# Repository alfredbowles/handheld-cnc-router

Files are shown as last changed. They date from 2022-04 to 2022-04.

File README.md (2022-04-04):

# Handheld CNC Router - Frebujar

The handheld CNC router is a project developed by Alfred Bowles, Shamanth Thenkan & Vincent Verster for a 2 month hardware seminar at the Institute for Advanced Architecture of Catalonia

The project aim is to develop a handheld CNC router which could be used for milling and inscribing into planar msheets of material.
The router will be hand-guided by the user while motors which control the position of the mill bit will activate to correct for the error made by the user between the actual and target position of the bit.

# Hardware & Materials #

All part drawings, milling files, and lasercutting files are found in the 'Manufacturing' dirctory.
BOM is found in the hardware folder

### Complete Assembly ###
* 4x Milled - Particle board, laminated on both sides : Thickness = 10mm
* 3x Lasercut - Plexiglass : Thickness = 6mm
* 2x Radial ball bearings : ID = 10mm
* 2x Radial ball bearings : ID = 50mm
* 2x Linear Bearings: ID = 10mm (For z-axis movement)
* 10mm thick calibrated steel rod
* 1x Shaft support
* 1x Threaded shaft bearing
* Various 3D Printed parts

LabeledPrototypeWhite

### Control, Power and Actuation ###
* 1x Raspberry Pi 4
* 1x Arduino Uno
* 1x 8MP Raspberry Pi Camera Module v2.1
* 1x Waveshare Raspberry Pi LCD Screen 3.5inch
* 3x Nema 17 Stepper Motors
* 3x A4988 Stepper Motor Drivers
* 1x 5v Fan
	


# Use Process

The user would either print or draw the desired pattern to be routed onto the piece of material. He would then activate the router and pass it over the material approximately following the printed path. The mounted camera which is aimed at the region around the bit tip will calculate the deviation needed to be made to account and correct for the user error and order the motors to move the mill head to the calculated point. As the user progresses through the material only the black areas which were printed or drawn will be removed and the piece would be complete.

# Control & Instructions

Since we are using a double cam mechanism we need to calculate how the bit would move with respect to the given motor rotations. In order to calculate the bit deviation, we use trigonometry and the law of cosines and sines.

### Angle Calculation ###
This code attempts to solve for those angles. (Angle calculation still to be optimized):
* Final_motion_calculation.py

The variables defined in the code are shown in the below diagram:
WhiteKinematics

### Adruino Motor control code ###
The file to convert the desired angles to microsteps and control the motors according to those steps
* Arduino_Motor_Control.ino

### Camera Calibration & Homography: ###
This file is run only once at the beginning in order to calibrate the camera and account for the exact distance and orientation of the camera with respect to the bit
* Homgraphy_Calibration.py

### Main Code - Line Tracking ###
The following file is used to detect object contours, calculate their centroids and fine the distance and angle between the camera center and the object center. These numbers are then outputted to the Final_motion_calculation.py file which then finds the desired motor angles.
* LineTracking.py

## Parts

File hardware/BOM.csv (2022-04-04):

Object | Details | Quantity | Unit Price | Subtotal | Supplier
Electronics
Raspberry Pi 3B+ |  | 1 | €48.00 | €48.00 | Mike
Arduino Uno |  | 1 | €0.00 | €0.00 | Pre-owned
Camera |  | 1 | €28.00 | €28.00 | Amazon
Stepper Motor - Nema 17 |  | 2 | €12.78 | €25.56 | Thingibox.com
Stepper Motor - Nema 17 with Thread |  | 1 | €34.85 | €34.85 | Thingibox.com
Stepper Drivers | A4988 Stepper Motor Driver | 3 | €4.00 | €12.00 | Amazon
LCD Screen |  | 1 | €35.00 | €35.00 | Amazon
Mechanical
Bolts | M2x15 | 4 | - | €10.00 | Ferreteria Bonet S.L
 | M3x15 | 4 | -
 | M3x25 | 8 | -
 | M3x30 | 2 | -
 | M4x15 | 10 | -
 | M4x20 | 10 | -
Nuts | M3 | 30 | -
 | M4 | 30 | -
Bearings | ID = 10 , OD = 26, T = 10 | 2 | €10.00 | €20.00 | Alaball Suministros Industriales S.L
 | ID = 50, OD = 65, T = 10 | 2 | €15.00 | €30.00 | 123rodamiento.es
Linear Bearings |  | 2 | €5.00 | €10.00 | Amazon
Rod Holders |  | 4 | €1.72 | €6.89 | Amazon
Thread Bearings and Internal Thread |  | 1 | €12.49 | €12.49 | Amazon
Raw Material
MDF - Laminated 10mm (800x600mm) |  | 1 | €10.00 | €10.00 | Servei Estacio
Steel Rod D=10mm (1m) |  | 1 | €10.00 | €12.41 | Thingibox.com
3D Printing
Total |  |  |  | €243.41

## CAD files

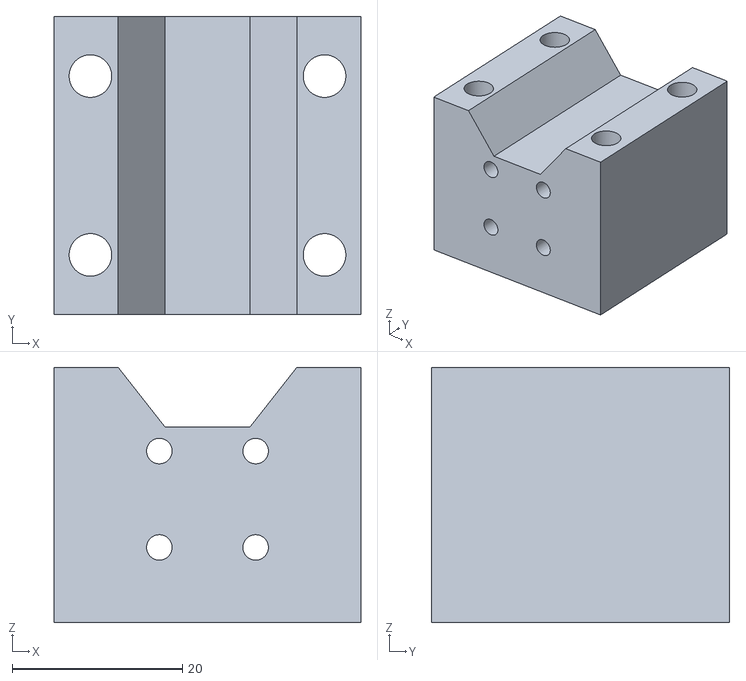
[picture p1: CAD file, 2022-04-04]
Manufacturing/3D Printed/LinearAdapter1.stl
36.0 x 35.0 x 30.0

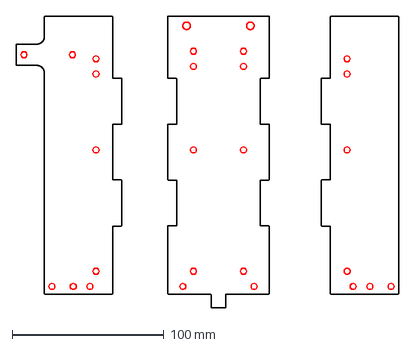
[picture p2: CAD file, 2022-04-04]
Manufacturing/Laser Cutting/Walls_6mm.dxf
252.0 x 192.0 mm

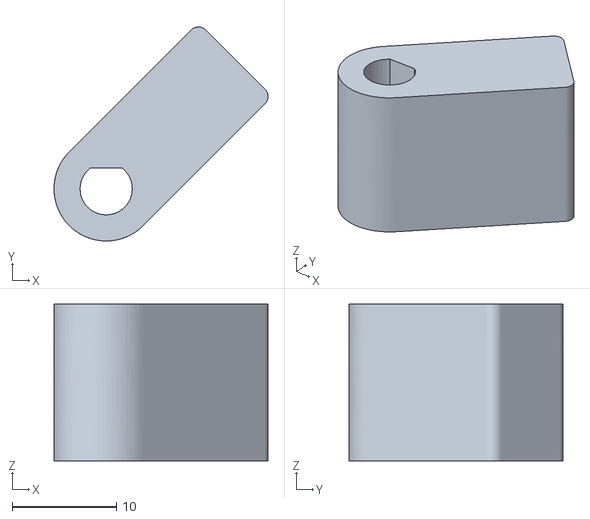
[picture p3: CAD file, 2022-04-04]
Manufacturing/3D Printed/MotorAdapter2.stl
20.5 x 20.5 x 15.0

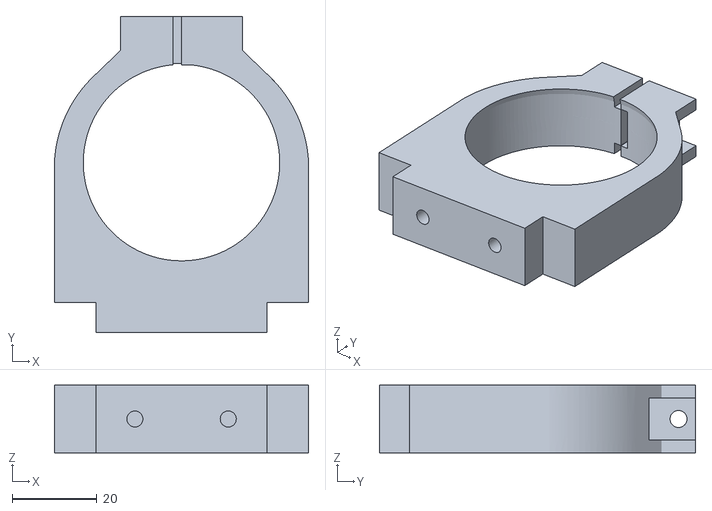
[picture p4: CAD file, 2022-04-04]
Manufacturing/3D Printed/DremelHolderBottom.stl
60.0 x 74.6 x 16.0

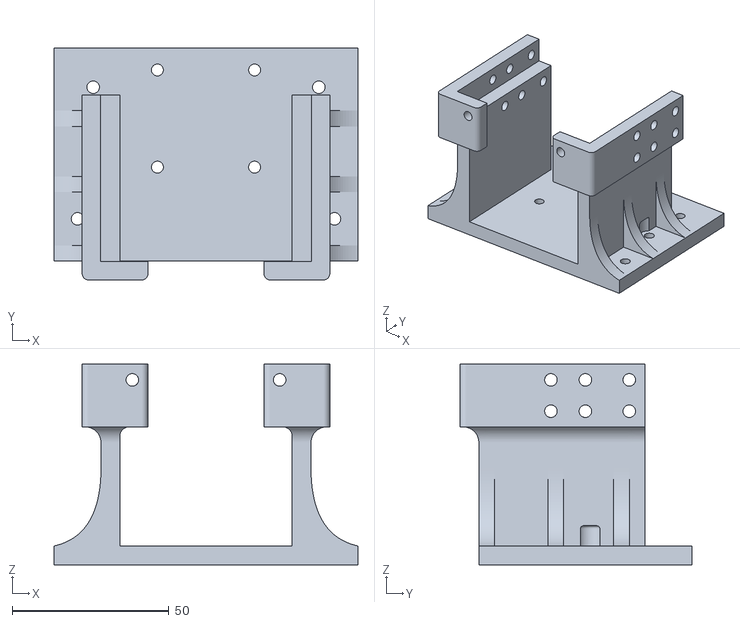
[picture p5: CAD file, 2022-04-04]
Manufacturing/3D Printed/MotorBase.stl
97.0 x 74.0 x 64.0

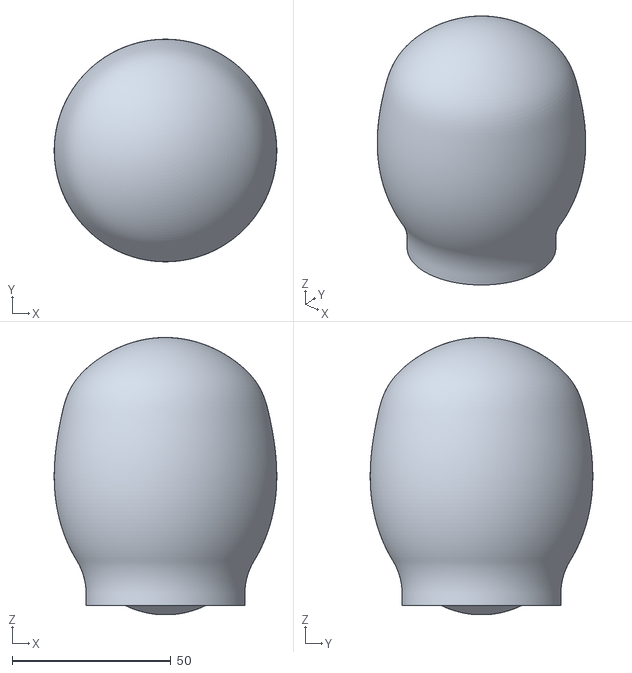
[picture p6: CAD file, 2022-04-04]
Manufacturing/3D Printed/Handle.stl
70.1 x 70.1 x 87.2

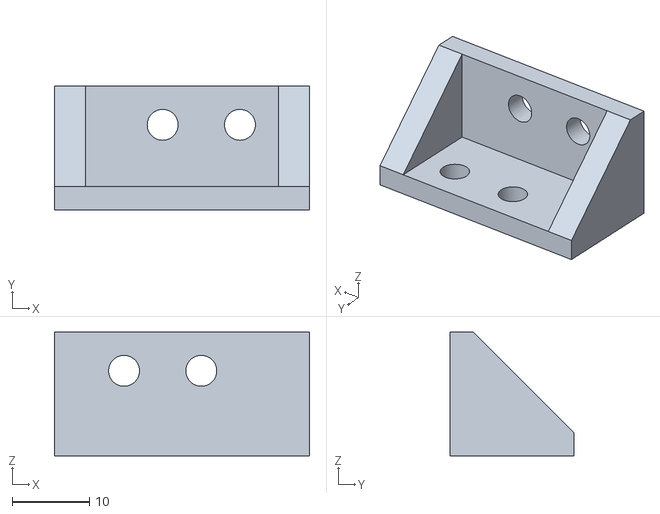
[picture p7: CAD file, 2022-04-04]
Manufacturing/3D Printed/AngleFrame.stl
33.0 x 16.0 x 16.0

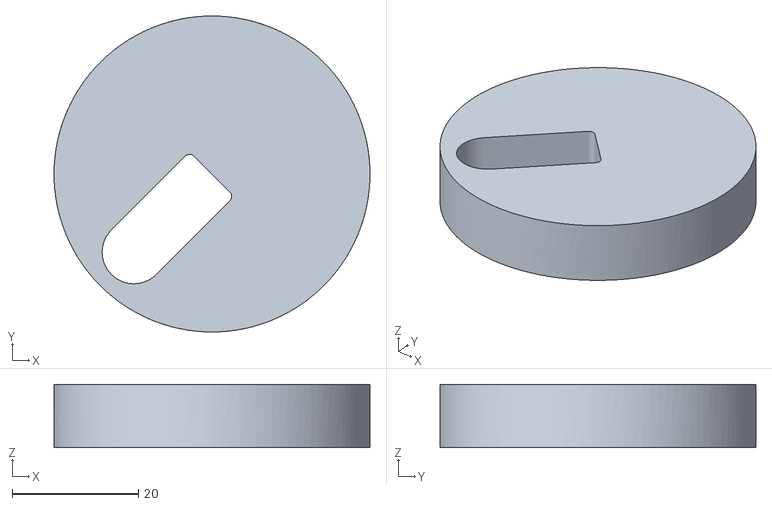
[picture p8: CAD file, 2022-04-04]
Manufacturing/3D Printed/Motot_Left_CAM.stl
50.0 x 50.0 x 10.0

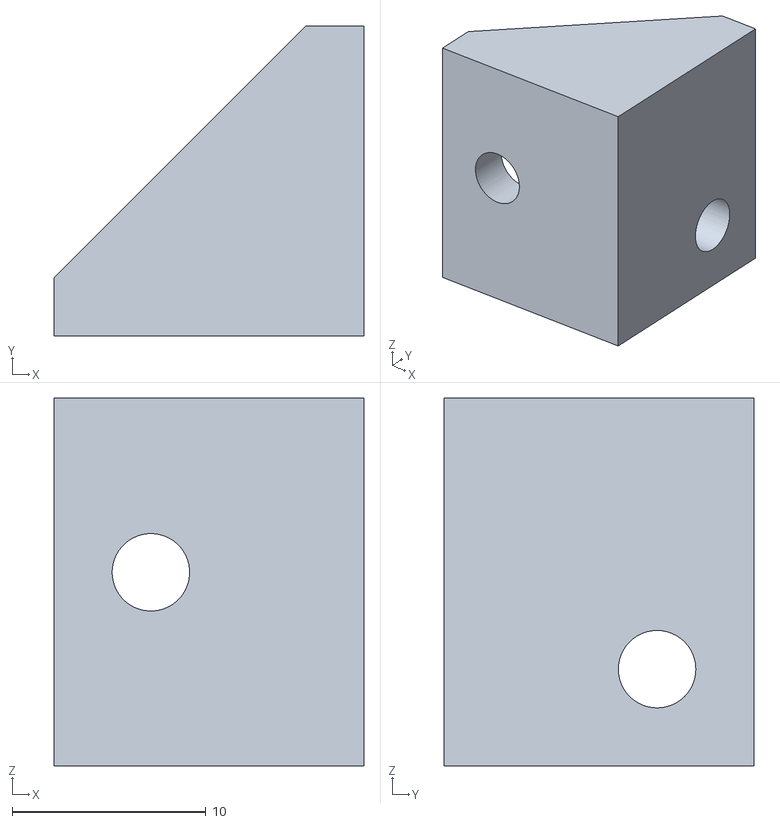
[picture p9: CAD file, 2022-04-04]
Manufacturing/3D Printed/AngleSupports.stl
16.0 x 16.0 x 19.0

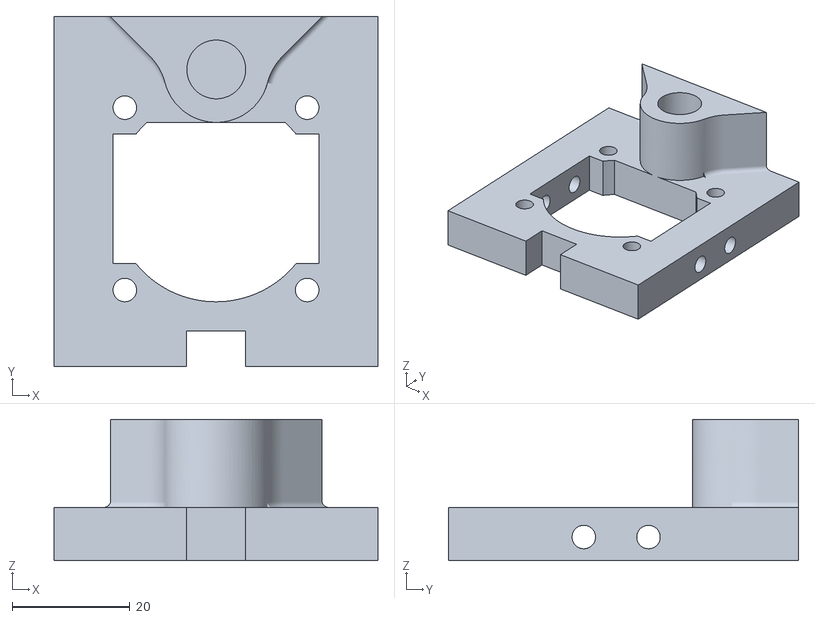
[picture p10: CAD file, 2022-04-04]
Manufacturing/3D Printed/MotorCover.stl
55.0 x 59.5 x 24.0

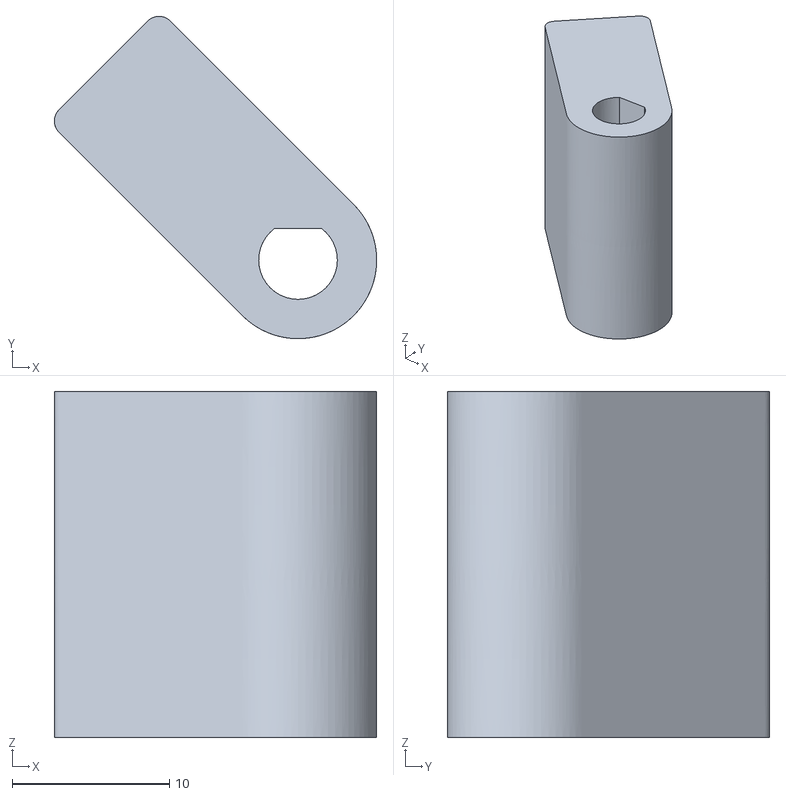
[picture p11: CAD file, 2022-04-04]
Manufacturing/3D Printed/Motor_Right_Adapter.stl
20.5 x 20.5 x 22.0

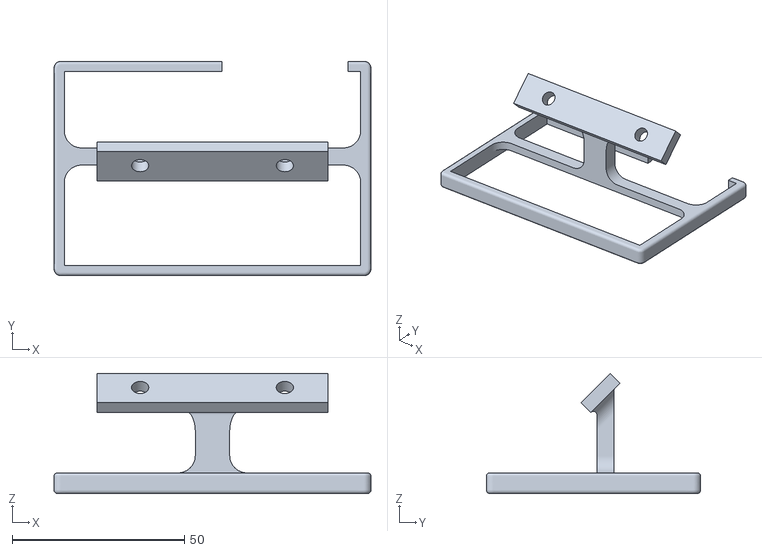
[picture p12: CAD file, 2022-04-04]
Manufacturing/3D Printed/ScreenHolder.stl
92.0 x 62.2 x 34.8

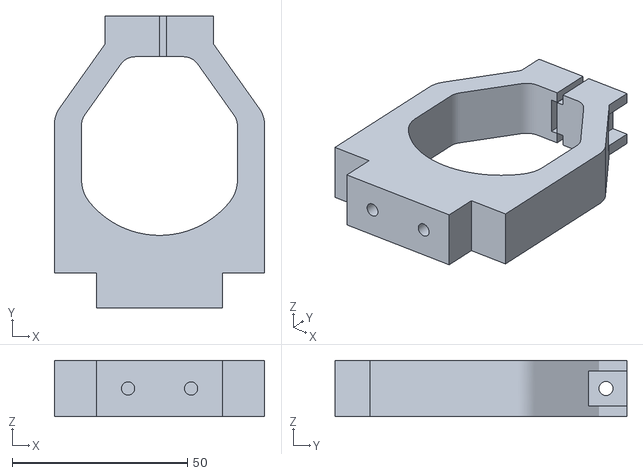
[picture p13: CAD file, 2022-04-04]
Manufacturing/3D Printed/DremelHolderTop.stl
60.0 x 83.4 x 16.0

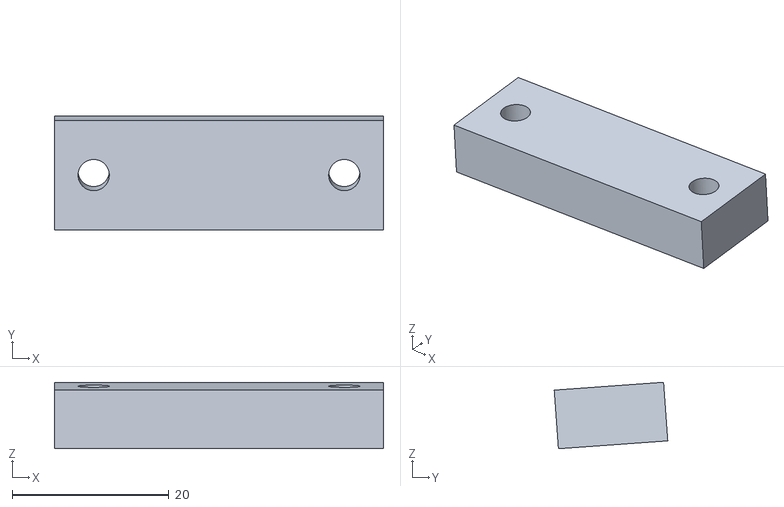
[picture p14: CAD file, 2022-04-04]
Manufacturing/3D Printed/BearingSpacer.stl
42.0 x 14.5 x 8.48

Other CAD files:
Manufacturing/3D Printed/Motot_Right_CAM.stl
Manufacturing/3D Printed/AngleFrame2.stl
Manufacturing/3D Printed/Motor_Left_Adapter.stl
Manufacturing/3D Printed/CameraHolder.stl
Manufacturing/3D Printed/AngleSupports2.stl
Manufacturing/3D Printed/DremelHolderBack.stl
Manufacturing/Laser Cutting/Walls_6mm.dwg
Manufacturing/Milling/MillingPlates_WithRhinoCAM.3dm

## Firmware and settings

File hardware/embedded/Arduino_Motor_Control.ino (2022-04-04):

# The following code is used to control the 3 Nema-17 stepper motors
# This code runs on the arduino uno and receives angles as strings through serial communication from the Raspberry Pi and converts them to microsteps to control the motors.

#define dirPin1 3
#define stepPin1 2
#define dirPin2 5
#define stepPin2 4
#define dirPin3 9
#define stepPin3 8
#define stepsPerRevolution 200

//float currentAngle = 0;
//float angle = 0;
//float incangle = 0;
float stepPerAngle = 1.8; // full step = 1.8
float tolerance = 1.0;
int pulseWidth = 1000;
int updatesPerLoop = 100;

int firstbracket;
int secondbracket;
int endnr;

float angle1;
float angle2;
float angle3;
float microStepFactor1 = 1.0;
float microStepFactor2 = 2.0;
float microStepFactor3 = 2.0;
//int numstep1;
//int numstep2;
//int numstep3;
//float n1;
//float n2;
//float n3;
float stepAngle1;
float stepAngle2;
float stepAngle3;
float currentAngle1;
float currentAngle2;
float currentAngle3;
String angle1st;
String angle2st;
String angle3st;
String firststring;
String secondstring;
String thirdstring;

// Debug iterations in update
//int counter = 0;

void setup() {
  Serial.begin(9600);
  // Sets the two pins as Outputs
  pinMode(stepPin1, OUTPUT);
  pinMode(dirPin1, OUTPUT);
  pinMode(stepPin2, OUTPUT);
  pinMode(dirPin2, OUTPUT);
  pinMode(stepPin3, OUTPUT);
  pinMode(dirPin3, OUTPUT);
  digitalWrite(dirPin1, HIGH);
  digitalWrite(dirPin2, HIGH);
  digitalWrite(dirPin3, HIGH);

}

void loop() {
  TryReadSerial();
  DebugAngles();
  for (int i = 0; i < updatesPerLoop; i++)
    UpdateMotors();
}
void TryReadSerial() {
  if (Serial.available() > 0) {
    String strdata = Serial.readStringUntil('\n');

    firstbracket = strdata.indexOf(";");
    secondbracket = strdata.indexOf(";", (firstbracket + 1));
    endnr = strdata.length();

    angle1st = strdata.substring(0, firstbracket);
    angle2st = strdata.substring((firstbracket + 1), secondbracket);
    angle3st = strdata.substring((secondbracket + 1), endnr);

    angle1 = angle1st.toFloat();
    angle2 = angle2st.toFloat();
    angle3 = angle3st.toFloat();
    //Serial.println("Angles Received");
  } else {
    //Serial.println("Angles Not Received");
  }
}
void DebugAngles() {
  //Serial.print("Angle1 ");
  Serial.print(angle1);
  Serial.print(",");
  //Serial.print("currentAngle1 ");
  Serial.print(currentAngle1);
  Serial.print(",");
  //Serial.print("Angle2 ");
  Serial.print(angle2);
  Serial.print(",");
  //Serial.print("currentAngle2 ");
  Serial.print(currentAngle2);
  Serial.print(",");
  //Serial.print("Angle3 ");
  Serial.print(angle3);
  Serial.print(",");
  //Serial.print("currentAngle3 ");
  Serial.println(currentAngle3);
}
void UpdateMotors() {
  stepAngle1 = 0;
  stepAngle2 = 0;
  stepAngle3 = 0;
  if (abs(currentAngle1 - angle1) > tolerance) {
    //    float n1;
    //    int numstep1;
    if (currentAngle1 < angle1) {
      digitalWrite(dirPin1, HIGH);
      //      n1 = angle1 - currentAngle1;
      //      numstep1 = n1 / stepPerAngle;
      stepAngle1 = stepPerAngle / microStepFactor1;
    }

    else if (currentAngle1 > angle1) {
      digitalWrite(dirPin1, LOW);
      //      n1 = currentAngle1 - angle1;
      //      if ( angle1 == 0) {
      //        n1 = currentAngle1;
      //      }
      //      numstep1 = round(n1 / stepPerAngle);
      stepAngle1 = -stepPerAngle / microStepFactor1;
    }

    //    for (int x = 0; x < numstep1; x++) {
    //        digitalWrite(stepPin1, HIGH);
    //        delayMicroseconds(pulseWidth);
    //        digitalWrite(stepPin1, LOW);
    //        delayMicroseconds(pulseWidth);
    //    }
    //    currentAngle1 = angle1;
    currentAngle1 += stepAngle1;
  }
  if (abs(currentAngle2 - angle2) > tolerance) {

    if (currentAngle2 < angle2) {
      digitalWrite(dirPin2, HIGH);
      //n2 = angle2 - currentAngle2;
      //numstep2 = n2 / stepPerAngle;
      stepAngle2 = stepPerAngle / microStepFactor2;
    }

    else if (currentAngle2 > angle2) {
      digitalWrite(dirPin2, LOW);
      //n2 = currentAngle2 - angle2;
      //if ( angle2 == 0) {
      //  n2 = currentAngle2;
      //}
      //numstep2 = n2 / stepPerAngle;
      stepAngle2 = -stepPerAngle / microStepFactor2;
    }

    //for (int x = 0; x < numstep2; x++) {
    //    digitalWrite(stepPin2, HIGH);
    //    delayMicroseconds(pulseWidth);
    
    //    digitalWrite(stepPin2, LOW);
    //    delayMicroseconds(pulseWidth);
    //}
    //currentAngle2 = angle2;
    currentAngle2 += stepAngle2;
  }
  if (abs(currentAngle3 - angle3) > tolerance) {

    if (currentAngle3 < angle3) {
      digitalWrite(dirPin3, HIGH);
      //n3 = angle3 - currentAngle3;
      //numstep3 = n3 / stepPerAngle;
      stepAngle3 = stepPerAngle / microStepFactor3;
    }

    else if (currentAngle3 > angle3) {
      digitalWrite(dirPin3, LOW);
      //n3 = currentAngle3 - angle3;
      //if ( angle3 == 0) {
      //  n3 = currentAngle3;
      //}
      //numstep3 = n3 / stepPerAngle;
      stepAngle3 = -stepPerAngle / microStepFactor3;
    }

    //for (int x = 0; x < numstep3; x++) {
    //    digitalWrite(stepPin3, HIGH);
    //    delayMicroseconds(pulseWidth);
    //    digitalWrite(stepPin3, LOW);
    //    delayMicroseconds(pulseWidth);
    
    //}
    //currentAngle3 = angle3;
    currentAngle3 += stepAngle3;
  }

  if (stepAngle1 != 0)
    digitalWrite(stepPin1, HIGH);
  if (stepAngle2 != 0)
    digitalWrite(stepPin2, HIGH);
  if (stepAngle3 != 0)
    digitalWrite(stepPin3, HIGH);
  if ((stepAngle1 != 0) || (stepAngle2 != 0) || (stepAngle3 != 0)){
    //counter +=1;
    delayMicroseconds(pulseWidth);
  }else {
    // Debug iterations in update
    //if (counter != 0){
    //  Serial.println();
    //  Serial.println(counter);
    //  Serial.println();
    //  counter = 0;
    //}
  }

  if (stepAngle1 != 0)
    digitalWrite(stepPin1, LOW);
  if (stepAngle2 != 0)
    digitalWrite(stepPin2, LOW);
  if (stepAngle3 != 0)
    digitalWrite(stepPin3, LOW);
  if ((stepAngle1 != 0) || (stepAngle2 != 0) || (stepAngle3 != 0)){
    delayMicroseconds(pulseWidth);
  }
  //delay(1);
}

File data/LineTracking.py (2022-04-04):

import cv2
import numpy as np
import math
import matplotlib.pyplot as plt

cap = cv2.VideoCapture(0)
# Set screen ratio
cap.set(3, 480)
cap.set(4, 2)

# Find Distance between object center and screen center
def distance(cx,cy,sx,sy):
    dist_x = abs(cx - sx)
    dist_y = abs(cy - sy)
    dist = math.sqrt(dist_x**2 + dist_y**2)
    return dist

#Read Frames
while True:
    ret, frame = cap.read()
    if frame is None:
        break
    #detect colour change
    l = 70
    h = 0
    low_b = np.uint8([l,l,l])
    high_b = np.uint8([h,h,h])

    #mask Colour Range and find contours
    mask = cv2.inRange(frame, high_b, low_b)
    contours, hierarchy = cv2.findContours(mask, 1, cv2.CHAIN_APPROX_SIMPLE)

    # Showing the final image. 
    dc=cv2.drawContours(mask,contours,0,(0,255,0),5)
    #Image Center
    (h, w) = frame.shape[:2]
    (sx, sy) = (w//2, h//2)
    if len(contours) > 0 :
            c = max(contours, key=cv2.contourArea)
            midPoints = []
            threshold = 60
            step = 5
            # print(type(c[0]))
            for j in range(0,len(c),step):
                point = c[j]
                midPoint = [0, 0]
                counter = 0
                for j2 in range(0, len(c), step):
                    point2 = c[j2]
                    pointsDist = distance(point[0][0],point[0][1],point2[0][0],point2[0][1]) 
                    if pointsDist < threshold:
                        midPoint[0] += point2[0][0]
                        midPoint[1] += point2[0][1]
                        counter += 1
                midPoints.append([np.array((int(midPoint[0]/counter),int(midPoint[1]/counter)))])
            midPoints = np.array(midPoints)
            print(midPoints)

            #To find centre of the line
            M = cv2.moments(midPoints)
            if M["m00"] !=0 :
                cx = int(M['m10']/M['m00'])
                cy = int(M['m01']/M['m00'])
                print("CX : "+str(cx)+"  CY : "+str(cy))
                cv2.circle(mask,(cx,cy),7, (0,255,255), 3)
                cv2.circle(mask, (sx, sy), 7, (255, 0, 255), -1)
                cv2.line(mask, (cx,cy), (sx, sy), (0,0,255), 4)
                dist = distance(cx,cy,sx,sy) 
                print(dist)
                font = cv2.FONT_HERSHEY_SIMPLEX
                cv2.putText(mask,"Distance = " +str(round(dist,3)),(50,70), font, .5,(255,255,255),2,cv2.LINE_AA)

                #conditions if the tool goes out of frame
                if cx >= 330 :
                    print("Move Left")
                    cv2.putText(mask,"Move Left!",(50,50), font, .5,(255,255,255),2,cv2.LINE_AA)
                    #GPIO PINS TO BE ADDED
                if cx > 300 and cx < 330 :
                    print("BRAVO!")
                    cv2.putText(mask,"On Track!",(50,50), font, .5,(255,255,255),2,cv2.LINE_AA)
                    #GPIO PINS TO BE ADDED
                if cx <=300 :
                    print("Move Right")
                    cv2.putText(mask,"Move Right!",(50,50), font, .5,(255,255,255),2,cv2.LINE_AA)
                
                #Center point
                cv2.circle(frame, (cx,cy), 5, (255,255,255), -1)
        
    #img = cv2.add(mask, blank)
    cv2.drawContours(frame, c, -1, (0,255,0), 1)
    cv2.drawContours(frame, midPoints, -1, (0,0,255), 1)

    cv2.imshow('Output',mask)
    cv2.imshow('frame',frame)

    #print(len(contours))
    if cv2.waitKey(1) & 0xff == ord('q'):   # 1 is the time in ms
        break

cap.release()
cv2.destroyAllWindows()

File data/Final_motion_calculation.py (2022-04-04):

import math as m
import matplotlib.pyplot as plt

# Plot links, motors, bit location and target location

def plotkinematics():
    plt.plot(x0, y0, '-d')
    draw_circle = plt.Circle((m1x, m1y), 17.5,fill=False, color="C3") 
    draw_circle2 = plt.Circle((m2x, m2y), 17.5,fill=False, color="C3")
    draw_circlebit = plt.Circle((bitx, bity), 3,fill=False, color="C5")
    plt.gcf().gca().add_artist(draw_circle)
    plt.gcf().gca().add_artist(draw_circle2)
    plt.gcf().gca().add_artist(draw_circlebit)
    plt.plot(x,y,'-o')
    plt.plot(m1x,m1y, '-o')
    plt.plot(m2x,m1y, '-o')
    plt.plot(bitx,bity, '-d')
    plt.plot(Ax, Ay, '-o')
    plt.plot(Bx, By, '-o')
    plt.plot([m1x,Ax],[m1y,Ay],'k-')
    plt.plot([m2x,Bx],[m2y,By],'k-')
    plt.plot([x,Ax],[y,Ay],'k-')
    plt.plot([x,Bx],[y,By],'k-')
    plt.plot([Ax,Bx],[Ay,By],'k-')
    
    plt.show()   

# Initialize

r1 = 17.5
r2 = 17.5
L1 = 110
L2 = 219.32
x0 = 90.16
y0 = -65.41
xn = -217.44
bitx = x0 + 63.64
bity = y0 - 63.64
dx = 5
dy = 5

(m1x, m1y) = (0,0)
(m2x, m2y) = (307.59,0)

x = x0 + dx
y = y0 + dy
xn = dx - (m2x - 90.16)

# Calculate angles ThetaL2 & ThetaL1 for the left side link
thetaL2 = -round(m.acos((x**2+y**2-r1**2-L1**2)/(2*r1*L1)),2)
thetaL1 = round(m.degrees(m.atan(y/x)-m.atan((L1*m.sin(thetaL2))/(r1+L1*m.cos(thetaL2)))),2)

# Calculate angles Thetar2 & ThetaR1 for the right side link
thetaR2 = round(m.acos((xn**2+y**2-r2**2-L2**2)/(2*r2*L2)),2)
thetaR1 = 180+round(m.degrees(m.atan(y/xn)-m.atan((L2*m.sin(thetaR2))/(r2+L2*m.cos(thetaR2)))),2)

# Calculate the position of points A, B and C based on the angles previously found
(Ax, Ay) = (r1*m.cos(m.radians(thetaL1)), r1*m.sin(m.radians(thetaL1)))
(Bx, By) = (m2x+r2*m.cos(m.radians(thetaR1)), m2y+r2*m.sin(m.radians(thetaR1)))
(Cx, Cy) = (x,y)

# Determine bit position with respect to motor angles (63.64 = distance between point C and the bit)
bitx, bity = (Cx + 63.64, Cy - 63.64 )

# The above was calculated to determine the forward kinematics relations between the motor input and the the bit tip. However the opposite also needs to be done
# since we need to infer the motor angles based on the bot location. Therefore we procedd to find the needed lengths L3, L4 & L5 and angles A,B,C & D:
L3 = abs(m.sqrt((Ay - By)**2 + (Ax-Bx)**2))
L4 = m.sqrt(63.64**2 + 63.64**2)
L5 = 200

angleA = round(m.degrees(m.acos((L1**2+L3**2-L2**2)/(2*L1*L3))),2)
angleB = round(m.degrees(m.acos((L2**2+L3**2-L1**2)/(2*L2*L3))),2)
angleC = round(m.degrees(m.acos((L1**2+L2**2-L3**2)/(2*L1*L2))),2)
angleD = round(m.degrees(m.acos((L2**2+L4**2-L5**2)/(2*L2*L4))),2)

# Calculate gamma

gamma = (By - Ay) / (Bx - Ax)

alpha0 = 44.99 + 114.24
alpha = angleA + angleC - alpha0

bit_target_x=bitx*m.cos(alpha)
bit_target_y=bity*m.sin(alpha)

print(f"L3 = {L3} ; L4 = {L4} ; L5 = {L5}")
print(f"Angle A = {angleA}\nAngle B = {angleB}\nAngle C = {angleC}\nAngle D = {angleD}\n")

motor1angle = thetaL1 - 45
motor2angle = thetaR1 - 135

print(f"Theta L1 = {thetaL1} ; Theta L2 = {round(m.degrees(thetaL2),2)}\nTheta R1 = {thetaR1} ; Theta R2 = {round(m.degrees(thetaR2),2)}")
print(f"Motor 1 Angle = {round(motor1angle,1)} ; Motor 2 Angle = {round(motor2angle,1)}")
plotkinematics()
